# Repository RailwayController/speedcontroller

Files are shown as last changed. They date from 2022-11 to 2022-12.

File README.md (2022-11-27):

<!--
SPDX-FileCopyrightText: 2022 Sidings Media <contact@sidingsmedia.com>
SPDX-License-Identifier: CC-BY-SA-4.0
-->

# Railway Controller - Speed controller

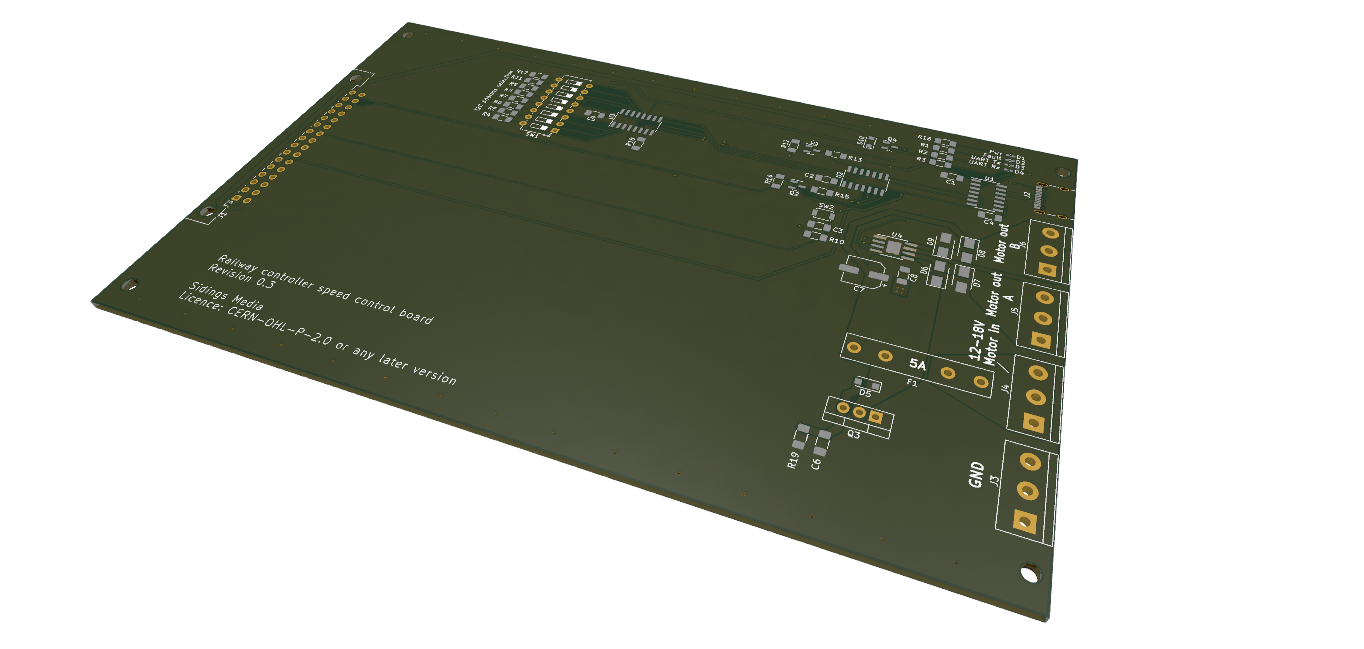
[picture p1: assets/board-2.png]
Render of speed control board


The speed control board is one of the most important control nodes in the
railway controller system as it is responsible for powering the trains in use.

The board is based upon the ATtiny84 and makes use of the DRV8872 motor driver
IC. A small amount of protection circuitry to protect against large over
voltages on the motor lines has been included. The board is designed to fit
inside a standard 3U eurocard enclosure with a depth of 160mm and a height of
100mm. The rear connector provides connectivity to the backplane to allow
communication between all nodes in the rack as well as to supply power to the
board.

The PCBs have been designed with 2 layers and with SMD components that should be
possible to hand solder with a small tip and some practice. An important note,
the boards have been designed acording to JLCPCB's design constraints, if you
are ordering from a different manufacturer, it is a good idea to make sure that
they support the same or better constraints.

This repository contains designs for the speed control board for
use with the railway controller system. Rendered versions of the schematics, for
example schematics in the PDF format, are included with the releases. Gerber
files are also included with releases. These have been generated to work with
JLCPCB but they should work with most other board manufacturers. 

## Licence
This repo uses the [REUSE](https://reuse.software) standard in order to
communicate the correct licence for the file. For those unfamiliar with
the standard the licence for each file can be found in one of three
places. The licence will either be in a comment block at the top of the
file, in a `.license` file with the same name as the file, or in the
dep5 file located in the `.reuse` directory. If you are unsure of the
licencing terms please contact
[contact@sidingsmedia.com](mailto:contact@sidingsmedia.com?subject=Railway%20Controller%20Licence).
All files committed to this repo must contain valid licencing
information or the pull request can not be accepted.

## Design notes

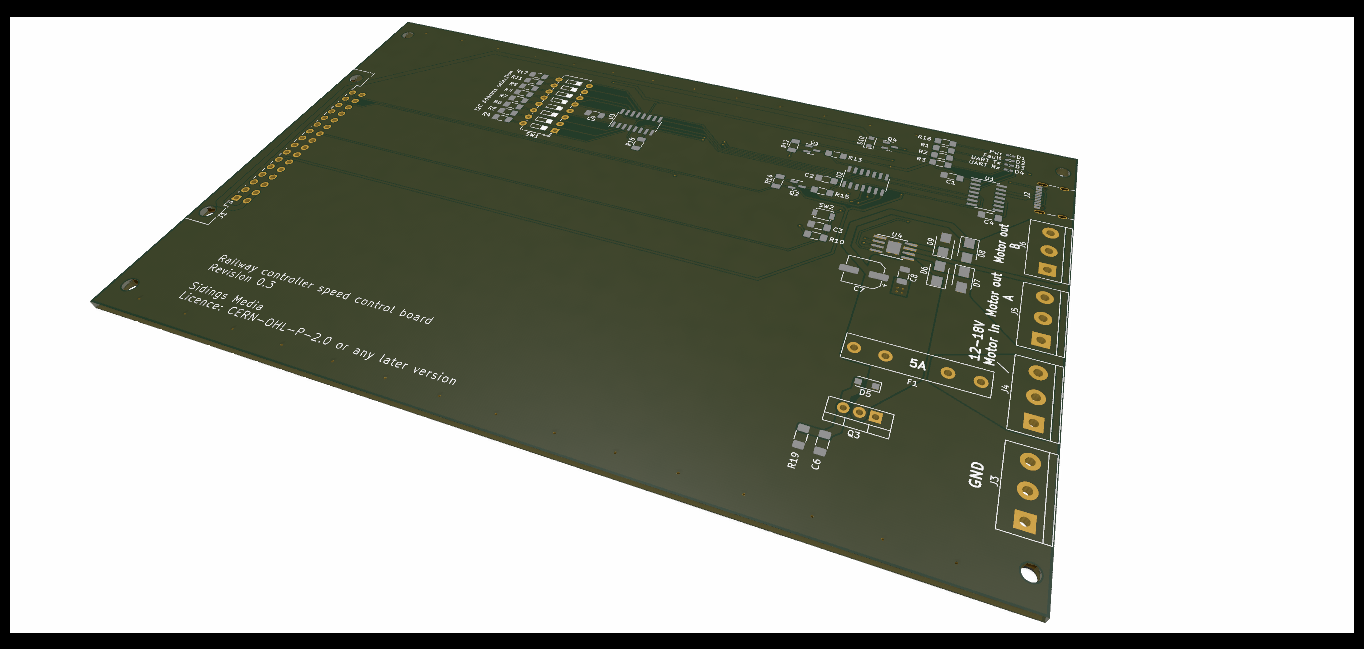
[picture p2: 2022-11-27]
assets/board-1.png

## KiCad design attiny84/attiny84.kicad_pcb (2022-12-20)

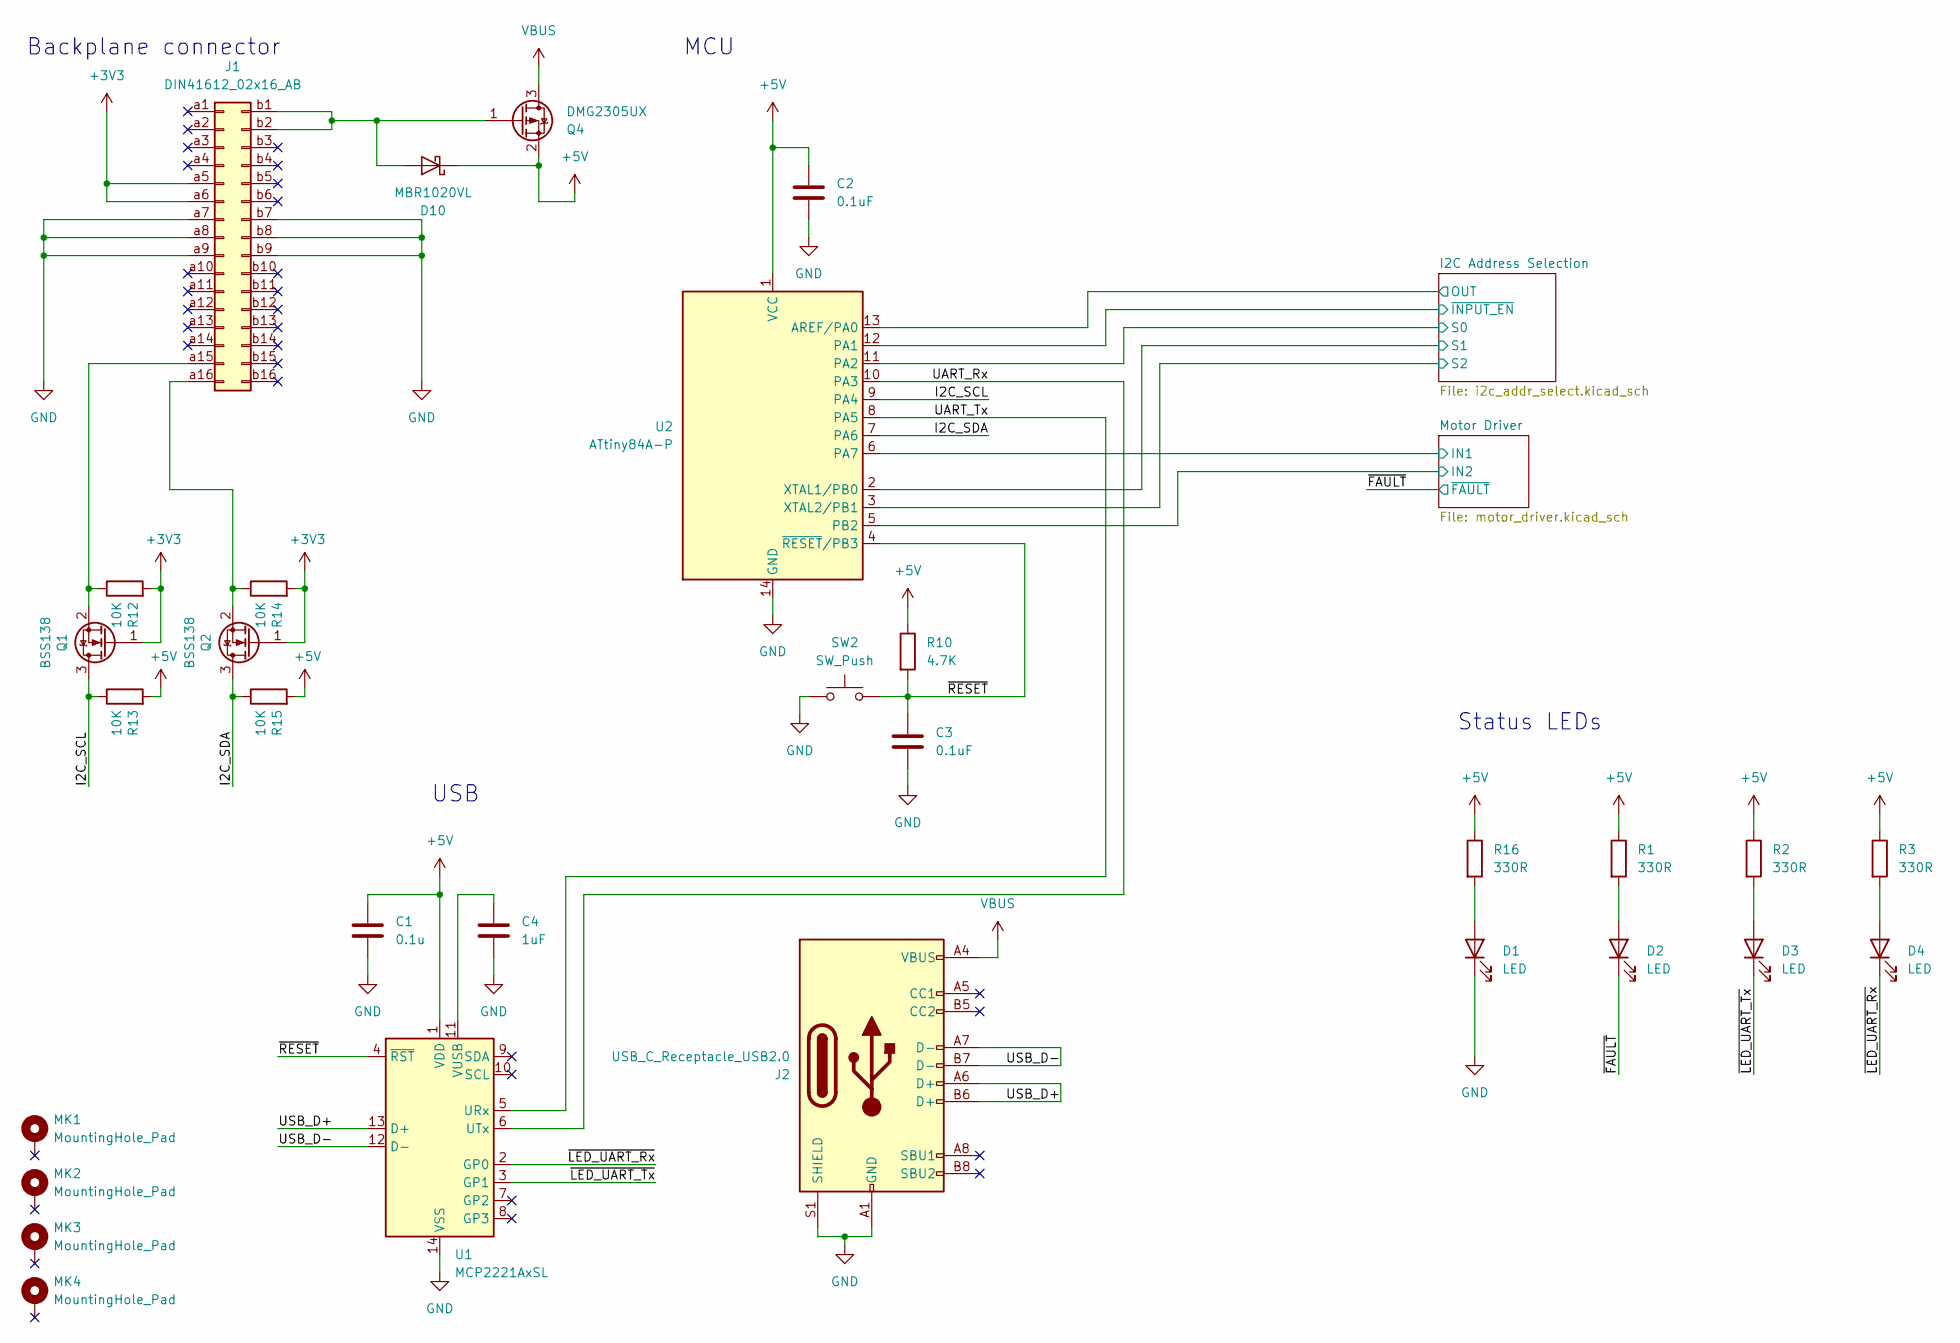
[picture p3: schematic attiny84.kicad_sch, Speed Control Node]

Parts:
C1: 0.1u; C_1206_3216Metric_Pad1.33x1.80mm_HandSolder
C2, C3: 0.1uF; C_1206_3216Metric_Pad1.33x1.80mm_HandSolder
C4: 1uF; C_1206_3216Metric_Pad1.33x1.80mm_HandSolder
D1, D2, D3, D4: LED; C_0402_1005Metric_Pad0.74x0.62mm_HandSolder
D10: MBR1020VL; D_SOD-123F
J1: DIN41612_02x16_AB; DIN41612_B2_2x16_Male_Horizontal_THT
J2: USB_C_Receptacle_USB2.0; USB_C_Receptacle_Palconn_UTC16-G
MK1, MK2, MK3, MK4: MountingHole_Pad; MountingHole_2.7mm
Q1, Q2: BSS138; SOT-23
Q4: DMG2305UX; SOT-23
R1, R2, R3, R16: 330R; R_1206_3216Metric_Pad1.30x1.75mm_HandSolder
R10: 4.7K; R_1206_3216Metric_Pad1.30x1.75mm_HandSolder
R12, R13, R14, R15: 10K; R_1206_3216Metric_Pad1.30x1.75mm_HandSolder
SW2: SW_Push; SW_SPST_B3U-1000P
U1: MCP2221AxSL; SOIC-14_3.9x8.7mm_P1.27mm
U2: ATtiny84A-P; SOIC-14_3.9x8.7mm_P1.27mm

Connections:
+3V3: J1.a5, J1.a6, Q1.1 (G), Q2.1 (G), R12.2, R14.2
+5V: C1.1, C2.1, D10.1 (K), Q4.2 (S), R1.1, R2.1, R3.1, R10.1, R13.2, R15.2, R16.1, U1.1 (VDD), U2.1 (VCC); also elsewhere on the board
/I2C Address Selection/OUT: U2.13 (AREF/PA0); also elsewhere on the board
/I2C Address Selection/S0: U2.11 (PA2); also elsewhere on the board
/I2C Address Selection/S1: U2.2 (XTAL1/PB0); also elsewhere on the board
/I2C Address Selection/S2: U2.3 (XTAL2/PB1); also elsewhere on the board
/I2C Address Selection/~INPUT_EN: U2.12 (PA1); also elsewhere on the board
/I2C_SCL: Q1.3 (D), R13.1, U2.9 (PA4)
/I2C_SDA: Q2.3 (D), R15.1, U2.7 (PA6)
/Motor Driver/IN1: U2.6 (PA7); also elsewhere on the board
/Motor Driver/IN2: U2.5 (PB2); also elsewhere on the board
/UART_Rx: U1.6 (UTx), U2.10 (PA3)
/UART_Tx: U1.5 (URx), U2.8 (PA5)
/USB_D+: J2.A6 (D+), J2.B6 (D+), U1.13 (D+)
/USB_D-: J2.A7 (D-), J2.B7 (D-), U1.12 (D-)
/~FAULT: D2.1 (K); also elsewhere on the board
/~LED_UART_Rx: D4.1 (K), U1.2 (GP0)
/~LED_UART_Tx: D3.1 (K), U1.3 (GP1)
/~RESET: C3.1, R10.2, SW2.2, U1.4 (~RST), U2.4 (~RESET/PB3)
GND: C1.2, C2.2, C3.2, C4.2, D1.1 (K), J1.a7, J1.a8, J1.a9, J1.b7, J1.b8, J1.b9, J2.A1 (GND), J2.A12 (GND), J2.B1 (GND), J2.B12 (GND), J2.S1 (SHIELD), SW2.1, U1.14 (VSS), U2.14 (GND); also elsewhere on the board
unnamed: C4.1, U1.11 (VUSB)
unnamed: D1.2 (A), R16.2
unnamed: D2.2 (A), R1.2
unnamed: D3.2 (A), R2.2
unnamed: D4.2 (A), R3.2
unnamed: D10.2 (A), J1.b1, J1.b2, Q4.1 (G)
unnamed: J1.a15, Q1.2 (S), R12.1
unnamed: J1.a16, Q2.2 (S), R14.1
VBUS: J2.A4 (VBUS), J2.A9 (VBUS), J2.B4 (VBUS), J2.B9 (VBUS), Q4.3 (D)

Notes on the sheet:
MCU
Backplane connector
Status LEDs
USB

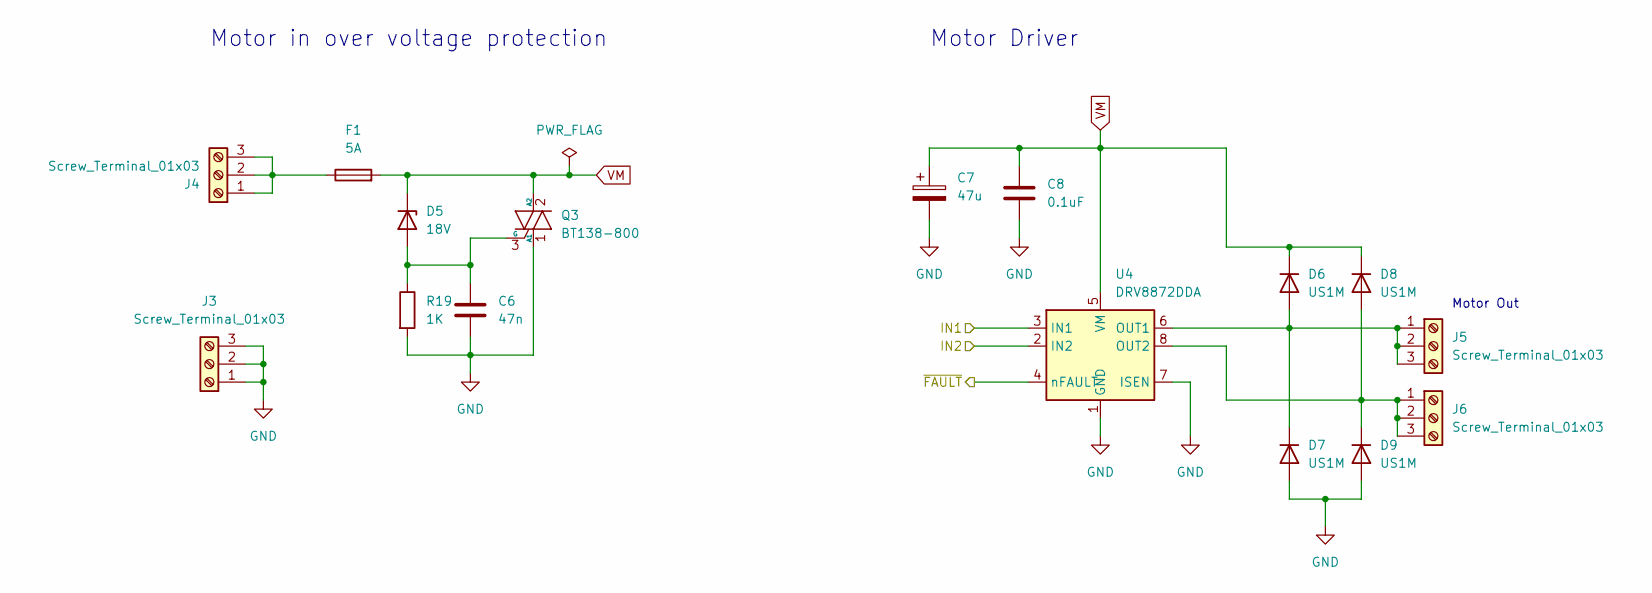
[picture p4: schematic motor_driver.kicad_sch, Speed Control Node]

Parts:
C6: 47n; C_1206_3216Metric_Pad1.33x1.80mm_HandSolder
C7: 47u; CP_Elec_6.3x5.7
C8: 0.1uF; C_1206_3216Metric_Pad1.33x1.80mm_HandSolder
D5: 18V; D_SOD-123F
D6, D7, D8, D9: US1M; D_SMA
F1: 5A; Fuseholder_Littelfuse_445_030_series_5x20mm
J3, J4, J5, J6: Screw_Terminal_01x03; TerminalBlock_bornier-3_P5.08mm
Q3: BT138-800; TO-220-3_Vertical
R19: 1K; R_1206_3216Metric_Pad1.30x1.75mm_HandSolder
U4: DRV8872DDA; Texas_HTSOP-8-1EP_3.9x4.9mm_P1.27mm_EP2.95x4.9mm_Mask2.4x3.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

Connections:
/Motor Driver/IN1: U4.3 (IN1); also elsewhere on the board
/Motor Driver/IN2: U4.2 (IN2); also elsewhere on the board
/~FAULT: U4.4 (nFAULT); also elsewhere on the board
GND: C6.2, C7.2, C8.2, D7.2 (A), D9.2 (A), J3.1, J3.2, J3.3, Q3.1 (A1), R19.2, U4.1 (GND), U4.7 (ISEN), U4.9 (GND); also elsewhere on the board
unnamed: C6.1, D5.2 (A), Q3.3 (G), R19.1
unnamed: D6.2 (A), D7.1 (K), J5.1, J5.2, J5.3, U4.6 (OUT1)
unnamed: D8.2 (A), D9.1 (K), J6.1, J6.2, J6.3, U4.8 (OUT2)
unnamed: F1.1, J4.1, J4.2, J4.3
VM: C7.1, C8.1, D5.1 (K), D6.1 (K), D8.1 (K), F1.2, Q3.2 (A2), U4.5 (VM)

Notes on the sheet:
Motor Driver
Motor Out
Motor in over voltage protection

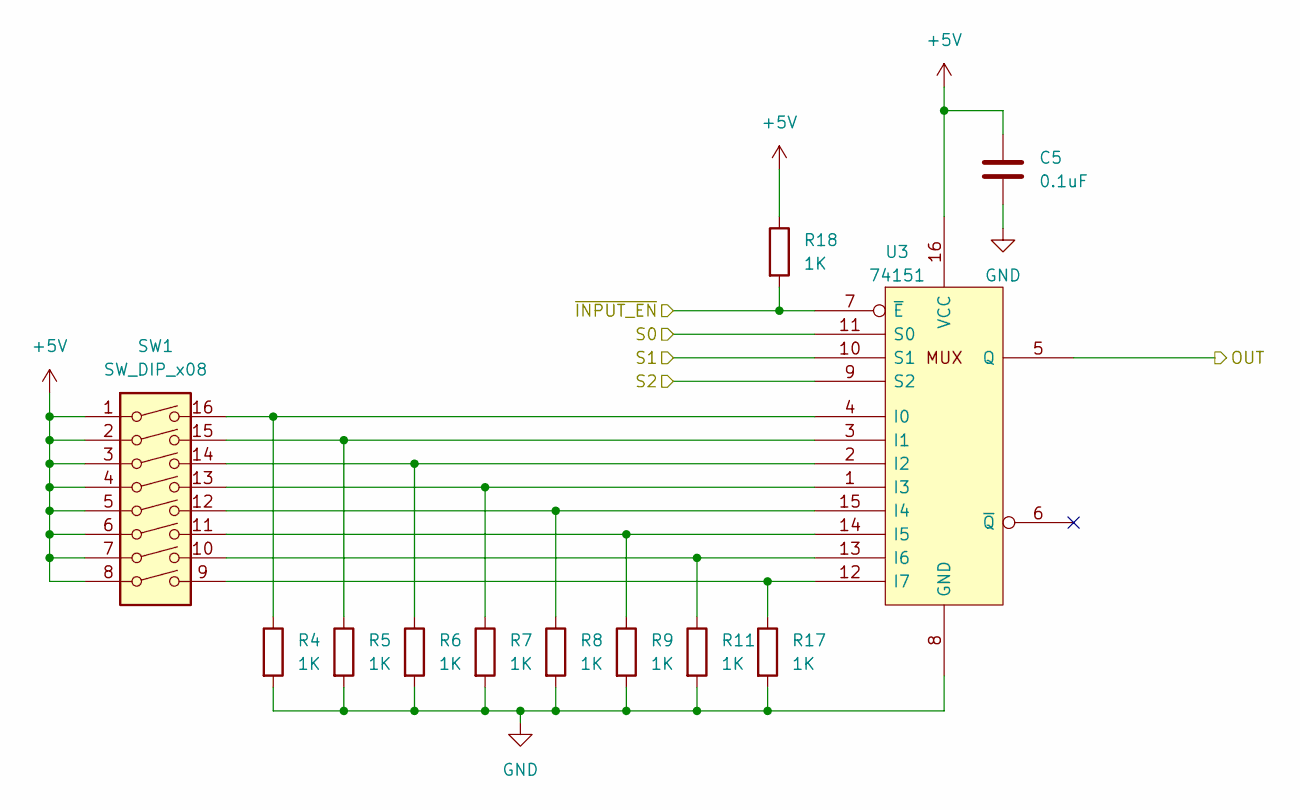
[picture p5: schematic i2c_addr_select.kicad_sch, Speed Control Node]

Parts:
C5: 0.1uF; C_1206_3216Metric_Pad1.33x1.80mm_HandSolder
R4, R5, R6, R7, R8, R9, R11, R17, R18: 1K; R_1206_3216Metric_Pad1.30x1.75mm_HandSolder
SW1: SW_DIP_x08; SW_DIP_SPSTx08_Slide_6.7x21.88mm_W7.62mm_P2.54mm_LowProfile
U3: 74151; SOIC-16_3.9x9.9mm_P1.27mm

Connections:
+5V: C5.1, R18.1, SW1.1, SW1.2, SW1.3, SW1.4, SW1.5, SW1.6, SW1.7, SW1.8, U3.16 (VCC); also elsewhere on the board
/I2C Address Selection/OUT: U3.5 (Q); also elsewhere on the board
/I2C Address Selection/S0: U3.11 (S0); also elsewhere on the board
/I2C Address Selection/S1: U3.10 (S1); also elsewhere on the board
/I2C Address Selection/S2: U3.9 (S2); also elsewhere on the board
/I2C Address Selection/~INPUT_EN: R18.2, U3.7 (~E); also elsewhere on the board
GND: C5.2, R4.2, R5.2, R6.2, R7.2, R8.2, R9.2, R11.2, R17.2, U3.8 (GND); also elsewhere on the board
unnamed: R4.1, SW1.16, U3.4 (I0)
unnamed: R5.1, SW1.15, U3.3 (I1)
unnamed: R6.1, SW1.14, U3.2 (I2)
unnamed: R7.1, SW1.13, U3.1 (I3)
unnamed: R8.1, SW1.12, U3.15 (I4)
unnamed: R9.1, SW1.11, U3.14 (I5)
unnamed: R11.1, SW1.10, U3.13 (I6)
unnamed: R17.1, SW1.9, U3.12 (I7)

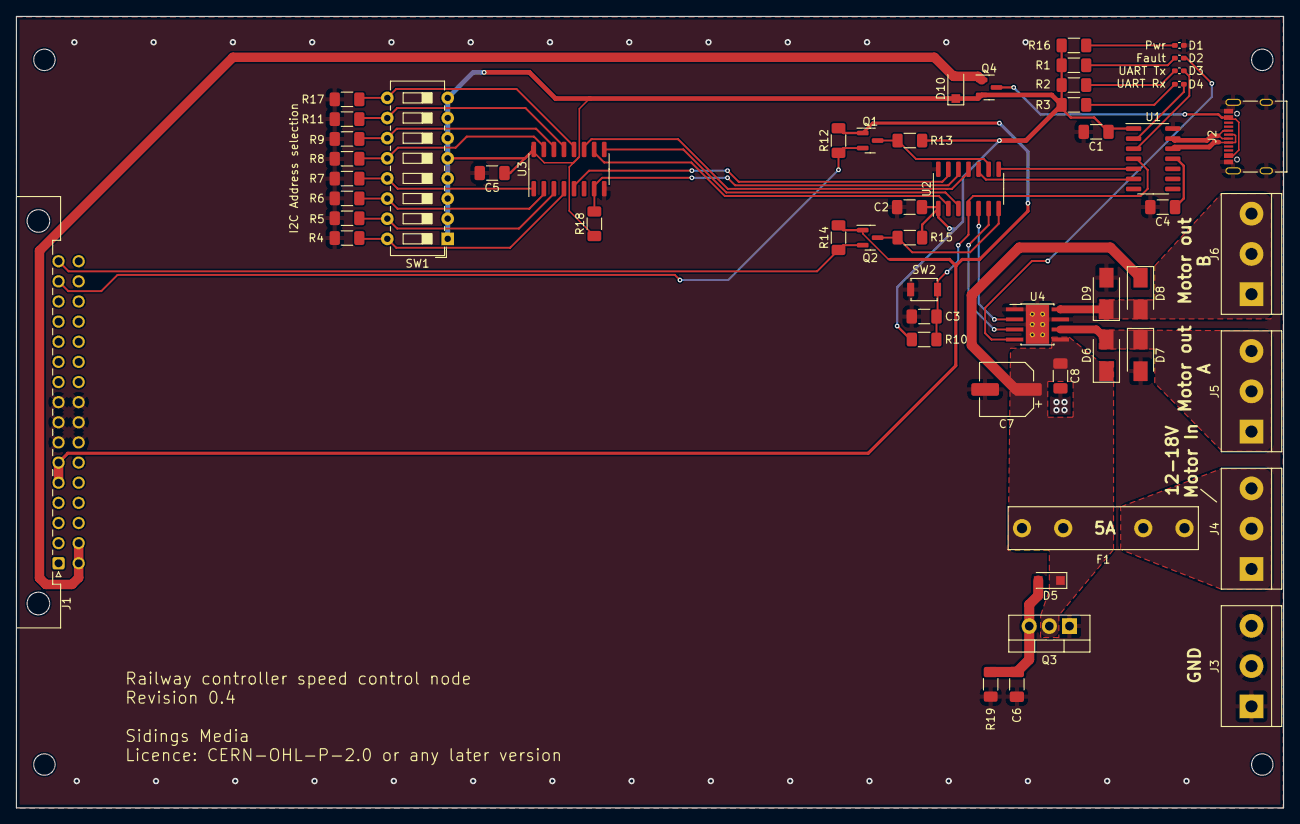
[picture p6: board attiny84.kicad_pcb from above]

Board: 2 copper layers, 159.9 x 99.9 mm, 58 parts (0 on the bottom side), 42 nets.

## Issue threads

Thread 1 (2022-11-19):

Change interface voltages to 3.3V

Computroniks, 2022-11-19:
All interface voltages need to be changed to 3.3V using logic level shifters. This includes, UART and I2C interfaces. This is because the logic level for the backplane is 3.3V.

Closed 2022-12-20.

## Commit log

2022-09-16 Created kicad project
    [attiny84-l298.kicad_pcb, attiny84-l298.kicad_sch]
2022-09-16 attiny84-l298 V0.1 Schematic
    [attiny84-l298.kicad_sch]
2022-09-16 Assigned footprints for attiny84-l298
    [attiny84-l298.kicad_sch]
2022-09-17 Fixed net label name
    [attiny84-l298.kicad_sch]
2022-09-17 V0.1 of attiny84-l298
    [attiny84-l298.kicad_pcb]
2022-09-17 Cleaned up schematic and fixed DRC errors
    [attiny84-l298.kicad_pcb, attiny84-l298.kicad_sch]
2022-09-17 Added PDF of schematic and interactive BOM
2022-11-26 Restructured project + changed motor driver IC
    The motor driver IC has been changed from the L298N to the DRV8872 due
    to it's smaller size, improved efficiency, lower cost and it's
    requirement for fewer external components. The banana plugs have also
    been removed in favour of screw terminals. A USB interface has also been
    added to allow for firmware to be updated by the end user. Additional
    LEDs have been added to indicate USB traffic and motor driver faults.
    [attiny84.kicad_pcb, attiny84.kicad_sch, i2c_addr_select.kicad_sch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]
2022-11-26 Removed old files
    [attiny84-l298.kicad_pcb, attiny84-l298.kicad_sch]
2022-11-26 Assigned footprints to all components
    [attiny84.kicad_sch, i2c_addr_select.kicad_sch, motor_driver.kicad_sch]
2022-11-26 Changed hole refference to match other schematics
    [attiny84.kicad_sch]
2022-11-26 Removed left over net label from IN1
    [attiny84.kicad_sch]
2022-11-26 Updated footprint of dip switch
    The footprint of SW1 has been changed from a generic DIP package to a
    specific DIP switch.
    [attiny84.kicad_sch, i2c_addr_select.kicad_sch]
2022-11-26 Designed PCB for rev 0.3
    The PCB has been designed for rev 0.3 of the circuit.
    [attiny84.kicad_pcb]
2022-11-27 Updated settings for gerber export
    [attiny84.kicad_pcb]
2022-12-20 Removed reset pin on backplane
    The connection between the reset pin and the backplane has been removed
    as it is not required. The reset pin on the backplane served no function
    as it would be near impossible to use in practice and was likely to
    cause issues surrounding pullup resistors if too many boards were added.
    As such, the link between the backplane and the IC reset pins has been
    removed, leaving only the reset button on the board.
    Fixes #1
    [attiny84.kicad_pcb, attiny84.kicad_sch, i2c_addr_select.kicad_sch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]
2022-12-20 Fixed revision + terminology on silk screen
    [attiny84.kicad_pcb]

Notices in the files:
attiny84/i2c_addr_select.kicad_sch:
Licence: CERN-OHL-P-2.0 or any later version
